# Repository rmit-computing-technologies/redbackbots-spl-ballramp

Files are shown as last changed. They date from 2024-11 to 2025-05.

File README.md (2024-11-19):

# RedbackBots 3D Ball Ramp

This is the official release of RedbackBot's 3D printable ball ramp for the RoboCup Soccer Standard Platform League (SPL).

Provided in this release are ready to 3D print files to be able to produce a ball ramp compatible with a 2024 rules compliant Soccer SPL ball.
The purpose of this design is for repeatable testing RoboCup SPL Soccer behaviours with a moving ball with varying speeds.
The ready-to-print files are located in the [`printing_files`](./printing_files) folder.
Additionally, the raw design files are provided in the [`design_files`](./design_files) folder.
Non-printed parts that are required to complete the build are detailed in the [parts list](./BOM.xlsx).

This design is provided 'as is'.
Pull requests and feature suggestions may be made through GitHub.

Before cloning this repository, you must read our license terms.

## Documentation

Printing and assembly instructions are found in the [SPL Ramp Manual PDF file](./SPL%20Ramp%20Manual.pdf).

Cite this repository and manual as:
```
Wiley, T., Peake, I., Babayigit, S., Ellis, T., George, B., Griffiths, S., Pham, M. H., Phillips, & C., Zhong Zhen, K. (2024). RedbackBots Soccer SPL Ball Ramp. AI Innovation Lab, School of Computing Technologies, RMIT University, Melbourne, Australia.
```

## About RedbackBots
RedbackBots is a undergraduate and postgraduate student team supported by the AI Innovation Lab in the School of Computing Technologies at RMIT University. The goals of RedbackBots are (1) a research project of the AI Innovation Lab, and (2) to provide education for RMIT students in applications of AI to autonomous robotics systems.
The release of our team's Soccer SPL software available at [GitHub](https://github.com/rmit-computing-technologies/redbackbots-coderelease).

You may contact the RedbackBots team at: stem.redbackbots@rmit.edu.au

## Support

For any issues or feature requests, feel free to contact us through our GitHub issues page or through the official RoboCup SPL discord or email stem.redbackbots@rmit.edu.au

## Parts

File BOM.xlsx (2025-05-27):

Component | Standard | Quantity | Description | Source
M3x6 BHCS | ISO 4762 / DIN 912 | 4 | Button head screws won't work due to its head size, Hex is preferred for its resilience against stripping | AliExpress (https://www.aliexpress.com/item/32810872544.html)
M3x8 BHCS | ISO 4762 / DIN 912 | 4 |  | AliExpress (https://www.aliexpress.com/item/32810872544.html)
M3x10 BHCS | ISO 4762 / DIN 912 | 4 |  | AliExpress (https://www.aliexpress.com/item/32810872544.html)
M3x4x5 Brass Heatset Insert |  | 12 | 18 is needed if extension is used, M3 insert, 4mm OD, 5mm Length (shorter length could still work) | AliExpress (https://www.aliexpress.com/item/1005003582355741.html)
Extensions extra optional |  |  | Add these numbers up for each extension that you are using
M3x6 BHCS | ISO 4762 / DIN 912 | 4 | Base extension screws
M3x8 BHCS | ISO 4762 / DIN 912 | 4 | Ramp extension screws
M3x4x5 Brass Heatset Insert |  | 4 | 4 is needed for a base extension
 |  | 4 or 6 | 4 is needed for a ramp extension if you are using a base extension, if you aren't then you need 6
Other tools needed
Soldering iron
Screwdriver with a hex head/hex key

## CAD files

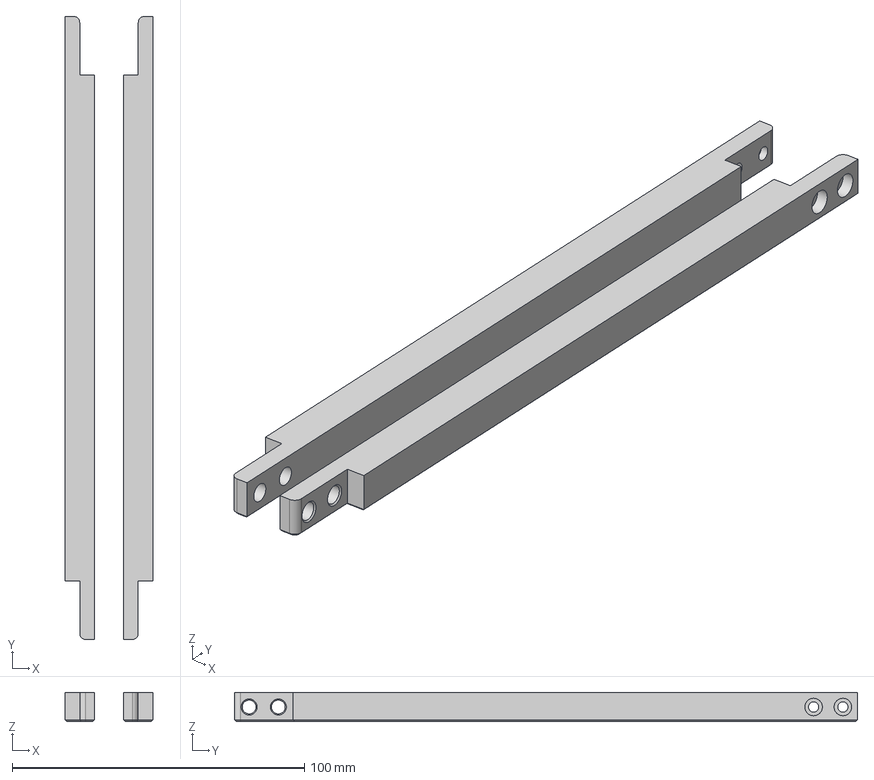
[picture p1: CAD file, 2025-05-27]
design_files/Base_Extension.step
30.0 x 213.0 x 10.0 mm

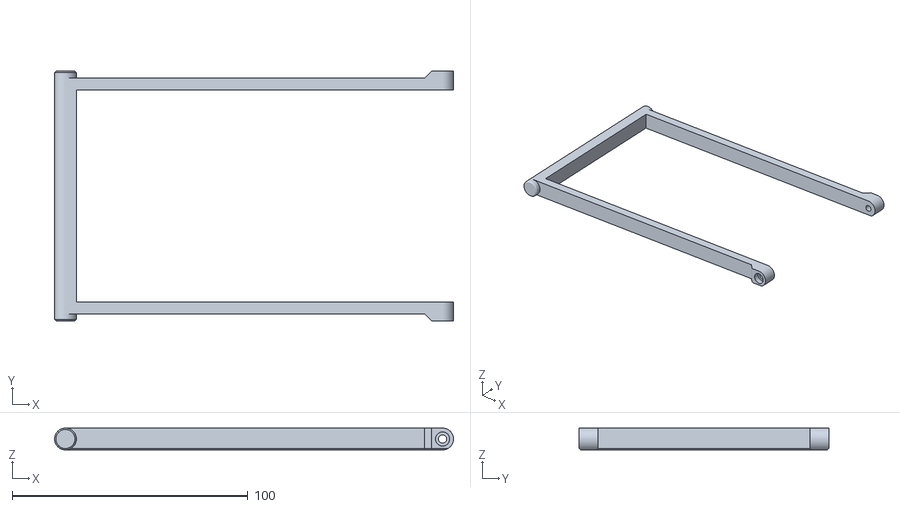
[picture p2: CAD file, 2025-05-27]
printing_files/Angle_Bar_160mm.stl
169.3 x 106.0 x 9.30

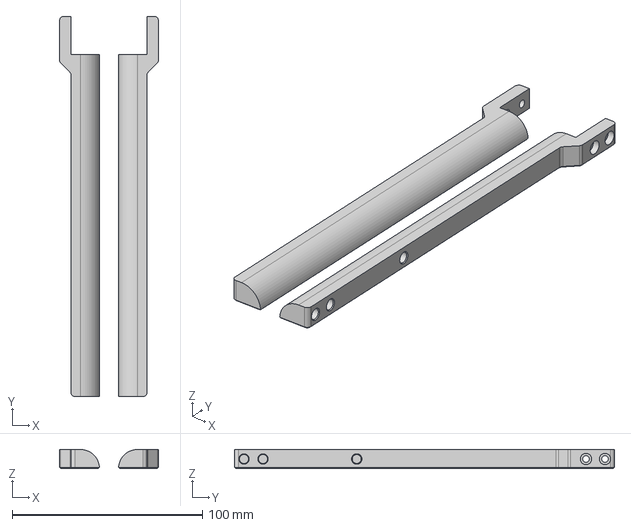
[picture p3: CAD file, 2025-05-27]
design_files/Ramp_Extension.step
52.0 x 200.0 x 10.0 mm

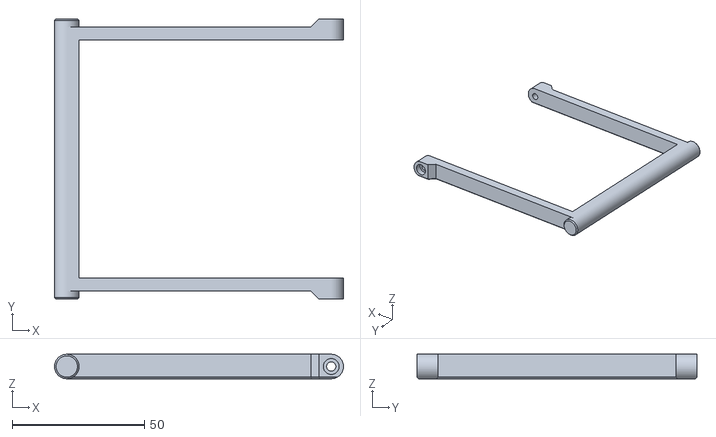
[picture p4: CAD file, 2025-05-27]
printing_files/Angle_Bar_100mm.stl
109.3 x 106.0 x 9.30

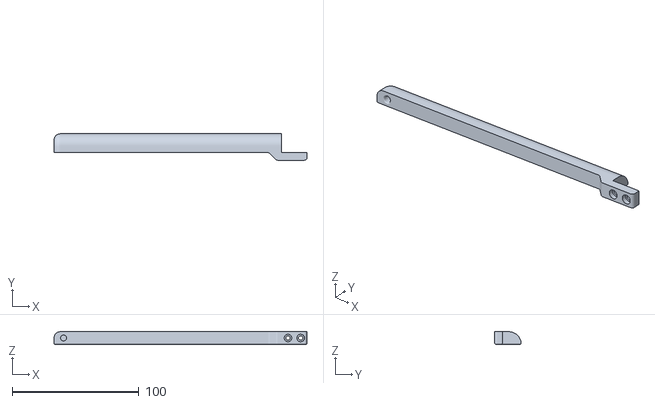
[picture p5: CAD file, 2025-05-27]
printing_files/Ramp_Right_Front.stl
200.0 x 21.0 x 10.0

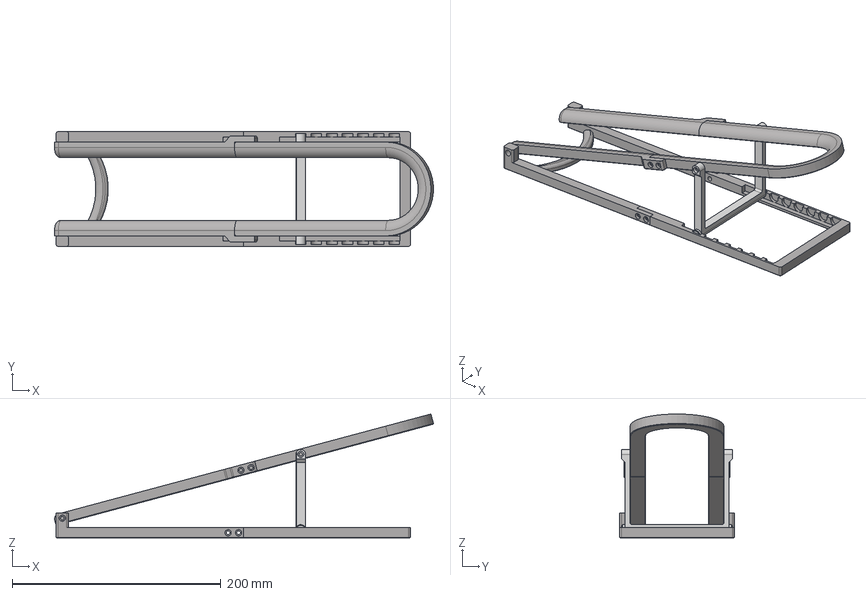
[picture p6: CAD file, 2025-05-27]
design_files/Ramp.step
363.5 x 110.0 x 118.9 mm

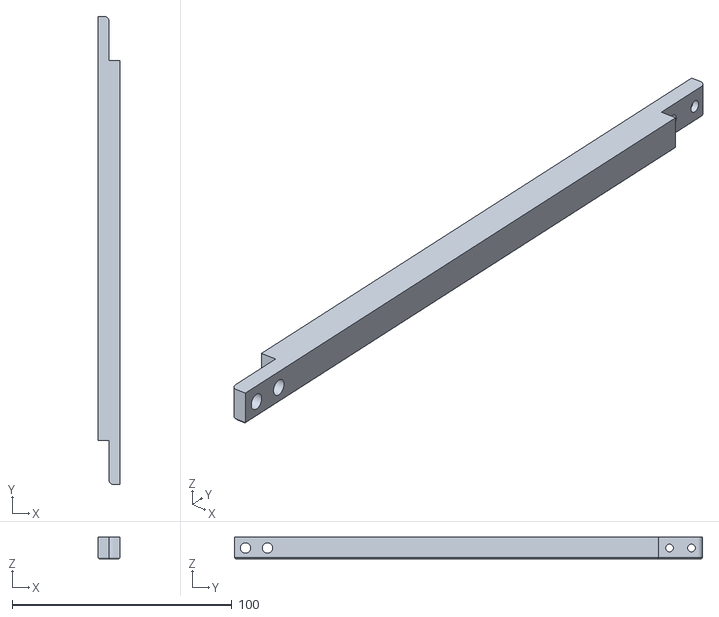
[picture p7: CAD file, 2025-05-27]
printing_files/Base_Left_Extension.stl
10.0 x 213.0 x 10.0

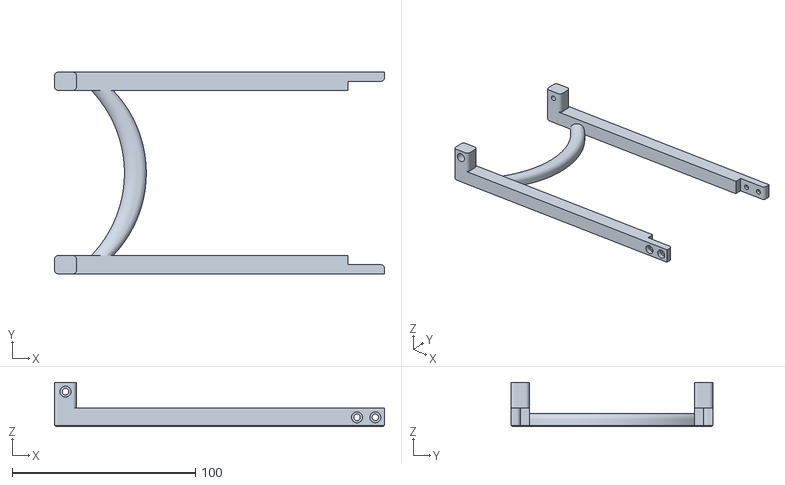
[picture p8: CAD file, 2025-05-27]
printing_files/Base_Front.stl
180.0 x 110.0 x 24.0

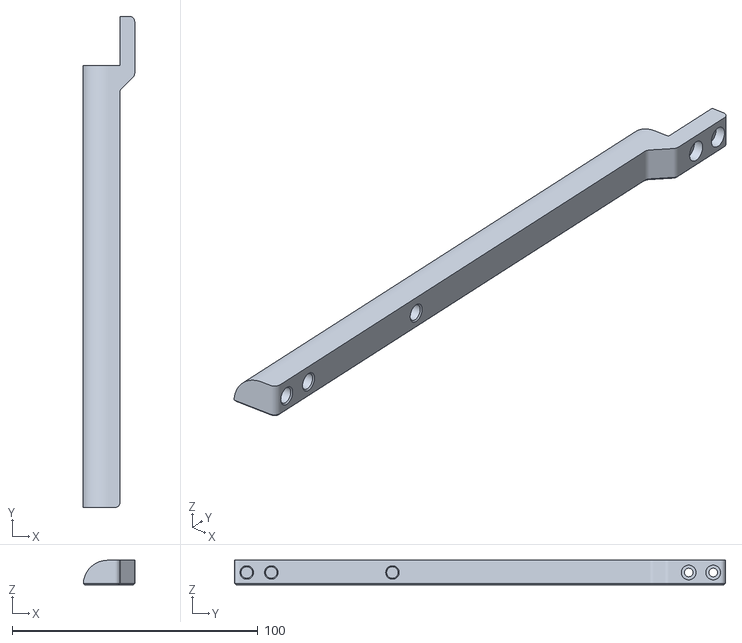
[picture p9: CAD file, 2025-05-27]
printing_files/Ramp_Right_Extension.stl
21.0 x 200.0 x 10.0

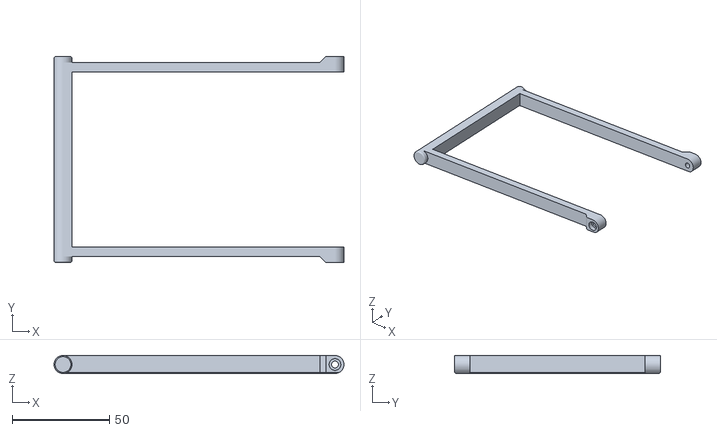
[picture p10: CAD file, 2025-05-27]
printing_files/Angle_Bar_140mm.stl
149.3 x 106.0 x 9.30

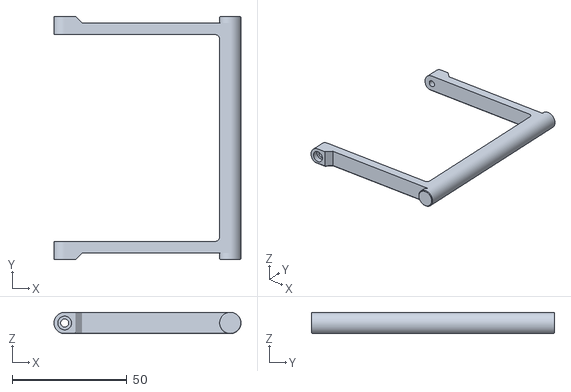
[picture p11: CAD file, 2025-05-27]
printing_files/Angle_Bar_72mm(Default).stl
81.4 x 106.0 x 9.30

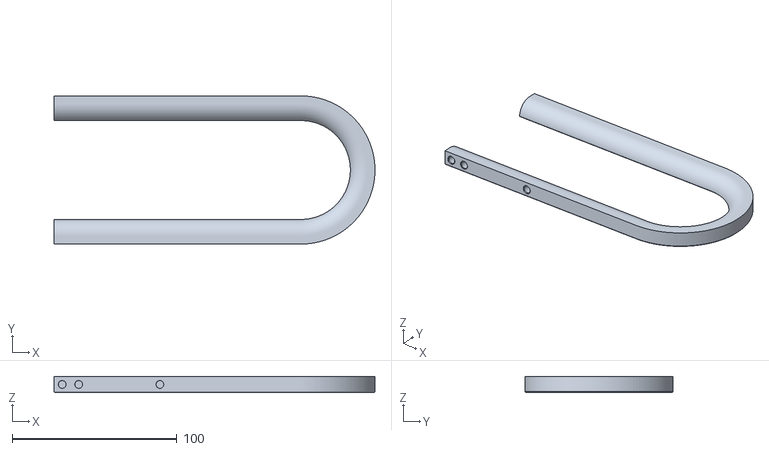
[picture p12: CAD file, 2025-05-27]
printing_files/Ramp_Rear.stl
195.0 x 90.0 x 10.0

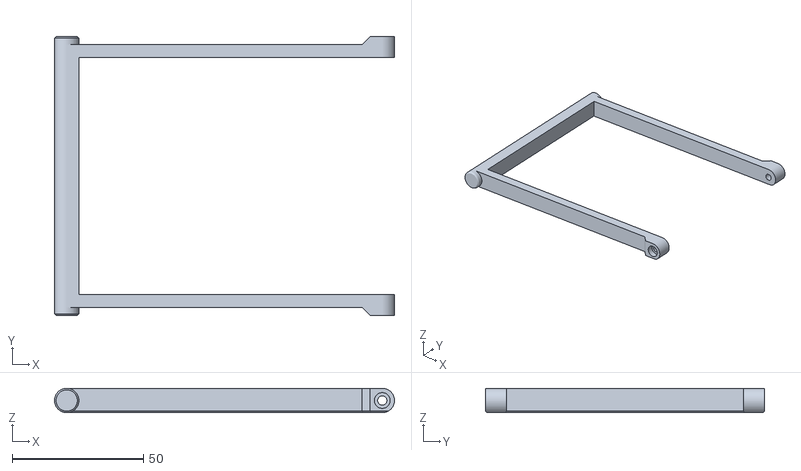
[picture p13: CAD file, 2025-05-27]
printing_files/Angle_Bar_120mm.stl
129.3 x 106.0 x 9.30

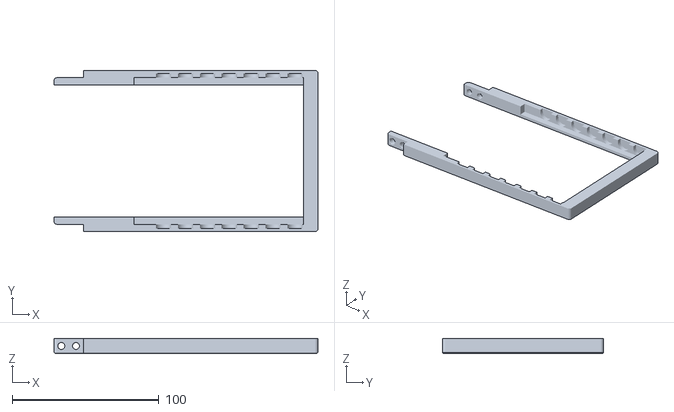
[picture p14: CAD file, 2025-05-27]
printing_files/Base_Rear.stl
180.0 x 110.0 x 10.0

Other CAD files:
design_files/Adjustable_Angle_Bar.step
printing_files/Ramp_Left_Front.stl
printing_files/Base_Right_Extension.stl
printing_files/Ramp_Left_Extension.stl
design_files/Adjustable_Angle_Bar.f3d
design_files/Base_Extension.f3d
design_files/Ramp.f3d
design_files/Ramp_Extension.f3d

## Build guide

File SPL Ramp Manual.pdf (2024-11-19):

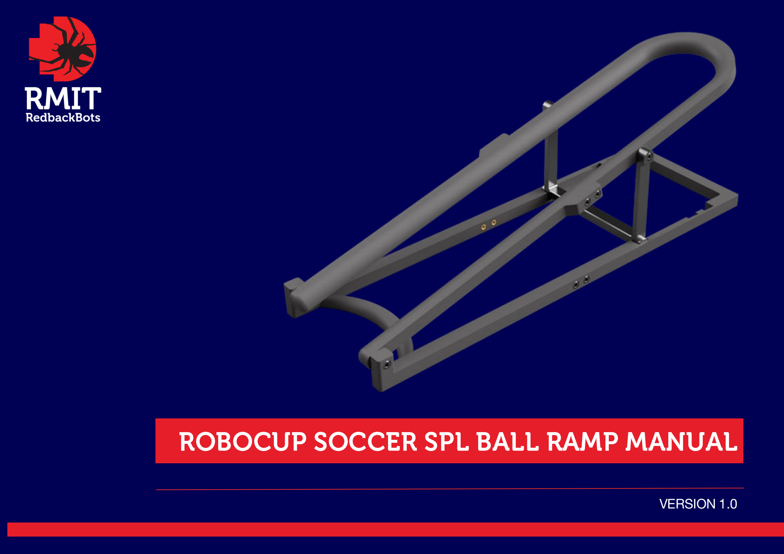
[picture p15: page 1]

### VERSION 1.0

TABLE OF CONTENTS | redbackbots.com

2

Introduction | 03
Hardware Reference | 05
Overview | 06
Heat Set Inserts | 08
Assembly | 10

2

INTRODUCTION | redbackbots.com

CREDITS
This work is a product of RedbackBots.

Original author
Minh Hoang Pham

Authors
Timothy Wiley
Ian Peake
Sera Babayigit
Tom Ellis
Benjamin George
Samuel Griffiths
Minh Hoang Pham
Clayton Phillips
Kurniawan Zhong Zhen

Copyright © 2024.
Artificial Intelligence Innovation Lab,
Centre for Industrial AI and Research Innovation (CIAIRI), School of Computing Technologies,
STEM College,
RMIT University.

rmit.edu.au/ciairi

INTRODUCTION | redbackbots.com

4

ROBOCUP RAMP
The ramp can be used to roll the standard SPL 100mm diameter ball. It has 3 adjustable angles: 5, 10, and 15. The design makes use of threaded inserts and Socket Head Cap Screws to assemble.

3D PRINTING PROCESS
Fused Deposition Modeling (FDM)

INFILL TYPE
Grid, Gyroid, Honeycomb, Triangle or Cubic

MATERIAL
PLA/PETG/ABS/ASA

INFILL PERCENTAGE
Recommended: 40%

LAYER HEIGHT
Recommended: 0.3mm

WALL COUNT
Recommended: 3

NOZZLE SIZE
Recommended: 0.6mm

SOLID TOP/BOTTOM LAYERS
Recommended: 3

4

HARDWARE REFERENCE | redbackbots.com

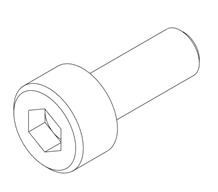
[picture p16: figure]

SOCKET HEAD CAP SCREW (SHCS) Metric fastener with a cylindrical head and hex drive.

ISO 4762

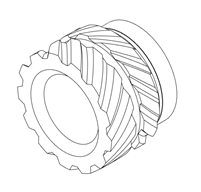
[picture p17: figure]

HEAT SET INSERT
Heat inserts with a soldering tip so that they melt the plastic when installed. As the plastic cools, it solidifies around the knurls and ridges on the insert for excellent resistance to both torque and pull-out.

redbackbots.com

### OVERVIEW

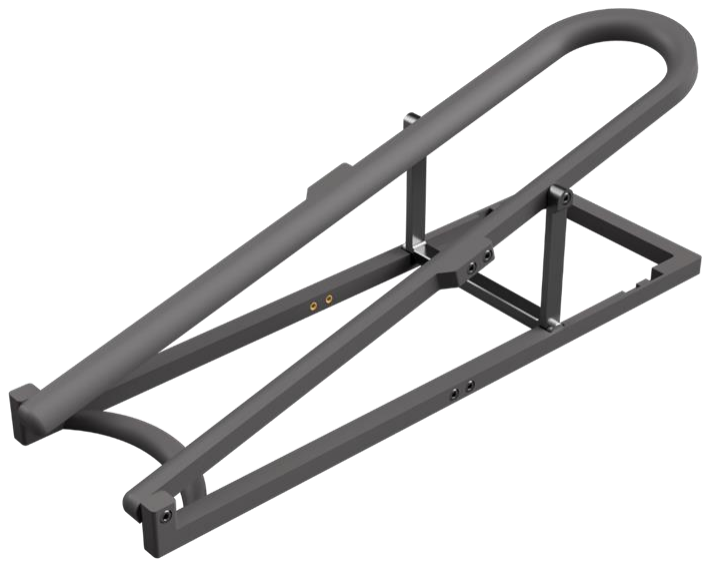
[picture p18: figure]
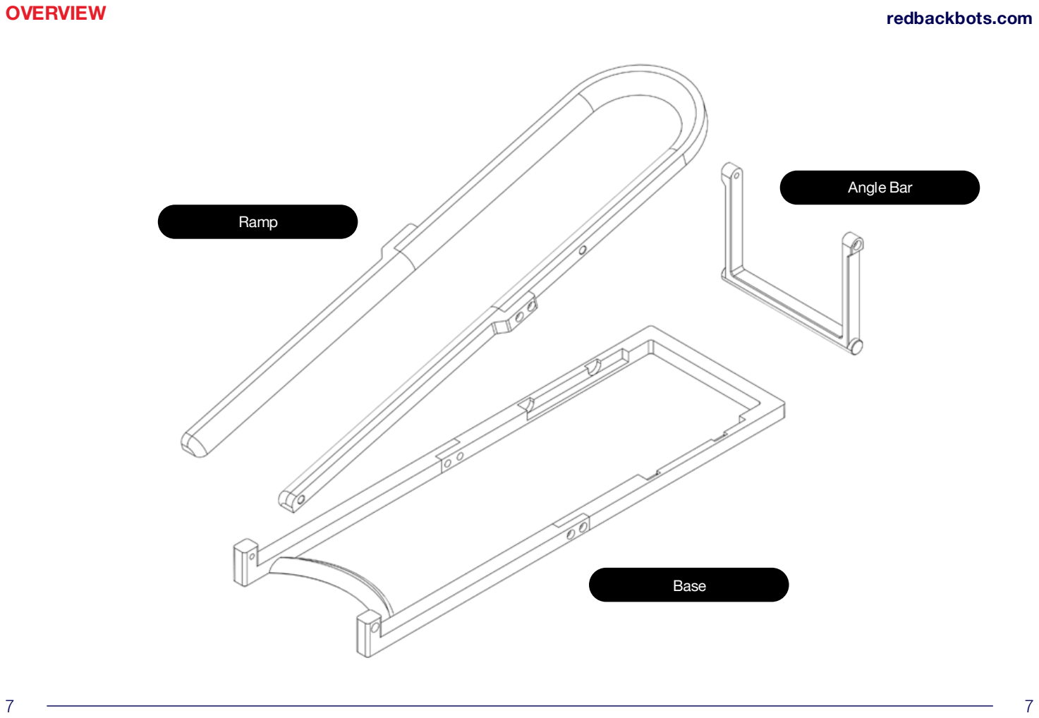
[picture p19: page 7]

OVERVIEW | redbackbots.com

Base

Ramp

Angle Bar

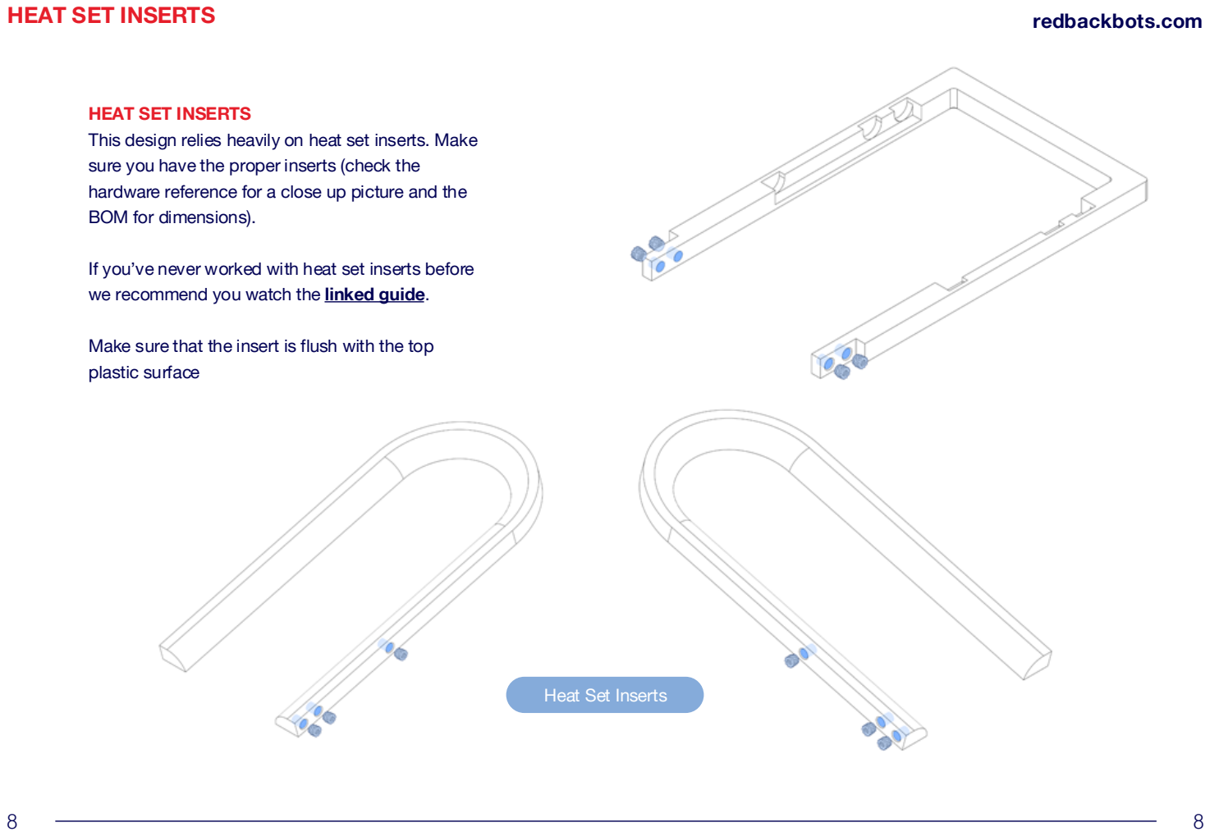
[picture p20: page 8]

HEAT SET INSERTS | redbackbots.com

HEAT SET INSERTS
This design relies heavily on heat set inserts. Make sure you have the proper inserts (check the hardware reference for a close up picture and the BOM for dimensions).

If you’ve never worked with heat set inserts before we recommend you watch the linked guide. (https://youtu.be/cyof7fYFcuQ?si=DbHLTQjiqBY7RvKz)

Make sure that the insert is flush with the top plastic surface

Heat Set Inserts

HEAT SET INSERTS | redbackbots.com

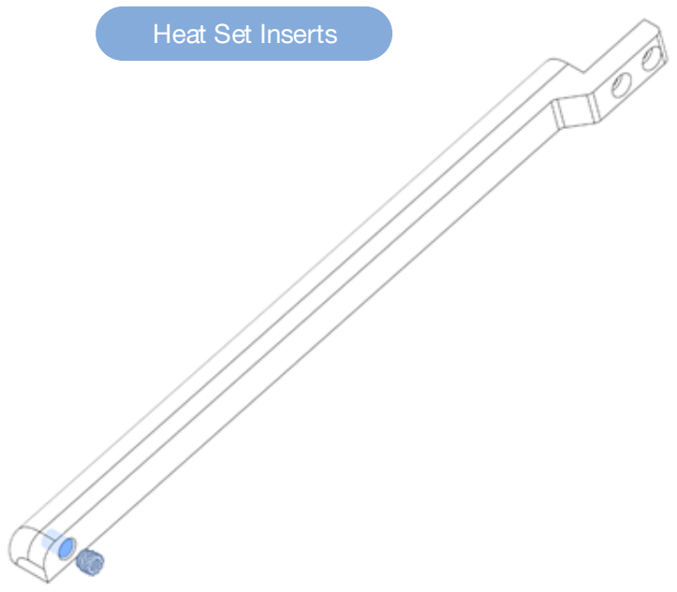
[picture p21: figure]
Heat Set Inserts
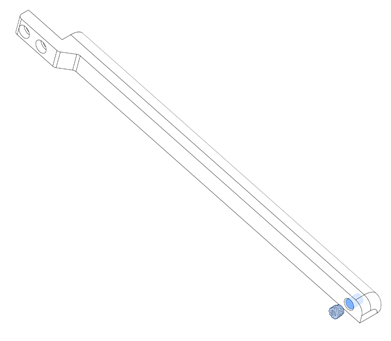
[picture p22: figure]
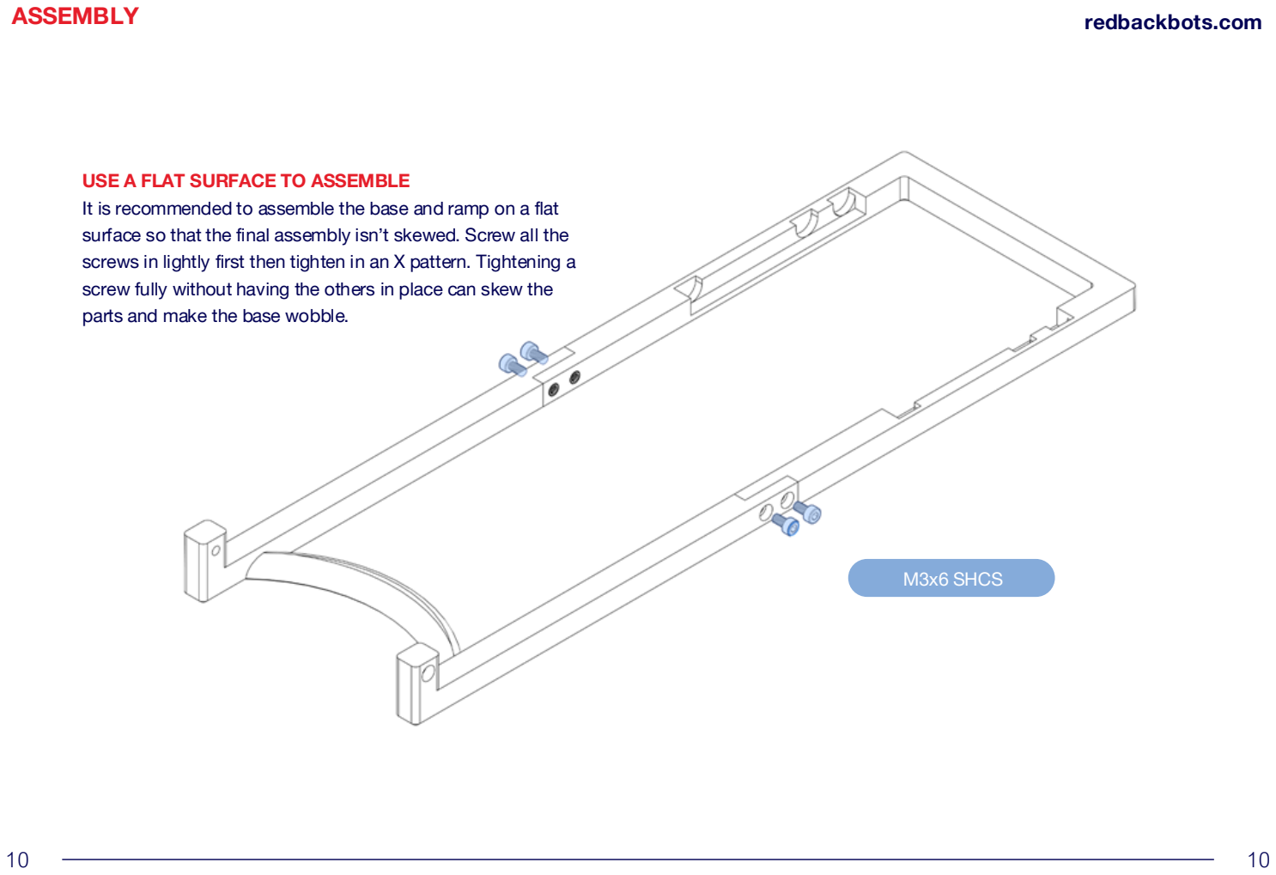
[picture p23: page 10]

ASSEMBLY | redbackbots.com

M3x6 SHCS

USE A FLAT SURFACE TO ASSEMBLE
It is recommended to assemble the base and ramp on a flat surface so that the final assembly isn’t skewed. Screw all the screws in lightly first then tighten in an X pattern. Tightening a screw fully without having the others in place can skew the parts and make the base wobble.

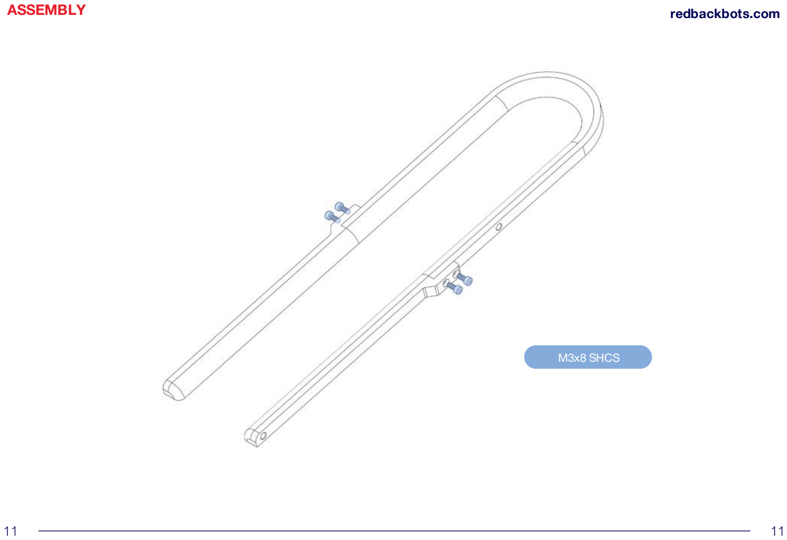
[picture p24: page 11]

ASSEMBLY | redbackbots.com

M3x8 SHCS

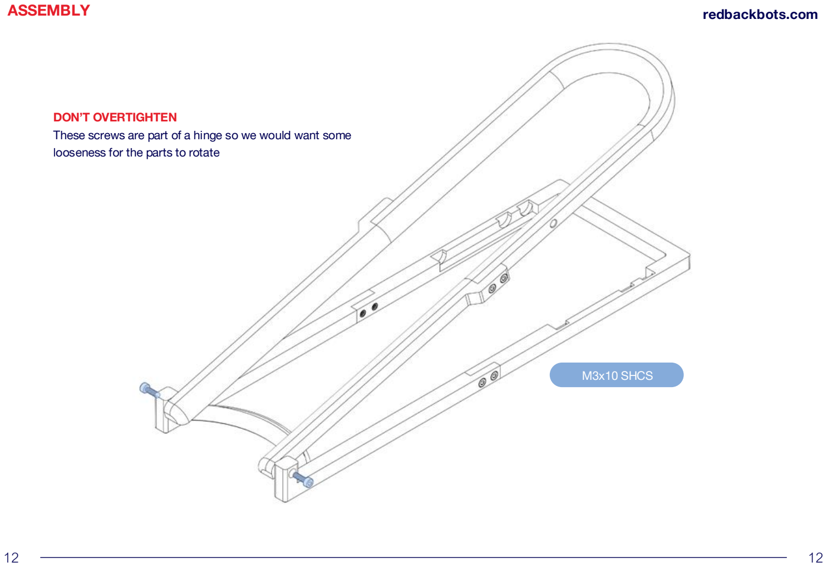
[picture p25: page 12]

ASSEMBLY | redbackbots.com

M3x10 SHCS

DON’T OVERTIGHTEN
These screws are part of a hinge so we would want some looseness for the parts to rotate

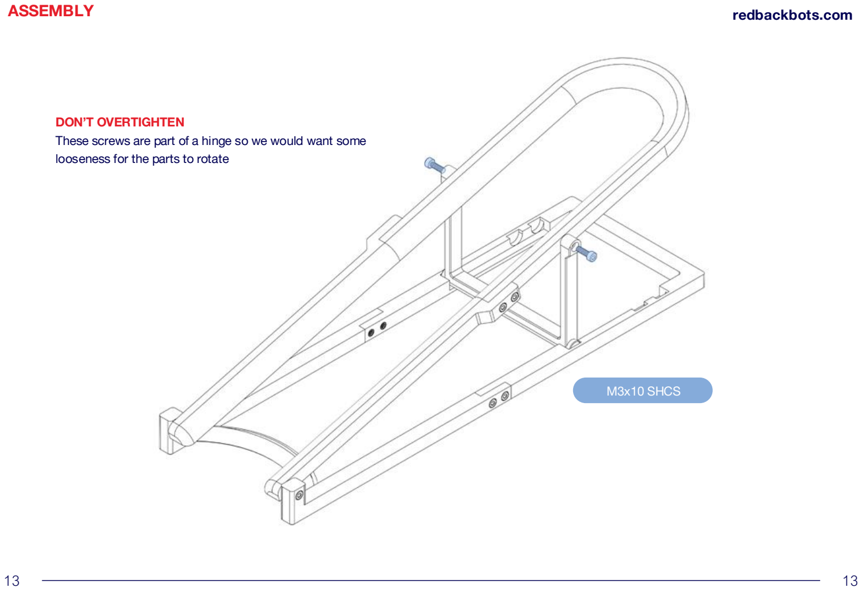
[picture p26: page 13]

ASSEMBLY | redbackbots.com

M3x10 SHCS

DON’T OVERTIGHTEN
These screws are part of a hinge so we would want some looseness for the parts to rotate

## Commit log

2024-11-19 RedbackBots SPL Ballramp initial release 2024
    [Angle_Bar.stl, BOM.xlsx, Base_Front.stl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]
2025-05-27 Extended features for RC2025 rule revisions
    [Adjustable_Angle_Bar.f3d, Adjustable_Angle_Bar.step, Angle_Bar.stl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]
